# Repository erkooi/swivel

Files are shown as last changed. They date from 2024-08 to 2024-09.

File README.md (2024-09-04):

# Model and animation of an F35B airplane swivel in OpenSCAD

For a video with animations of the swivel and more information please also check my channel "Eric Kooistra - Hobby" on YouTube: https://www.youtube.com/@EricKooistra-Hobby

## 1 3D-printed swivel model
The swivel model consists of four identical tube segments, one as input tube, two for the mid tube, and one as output tube.

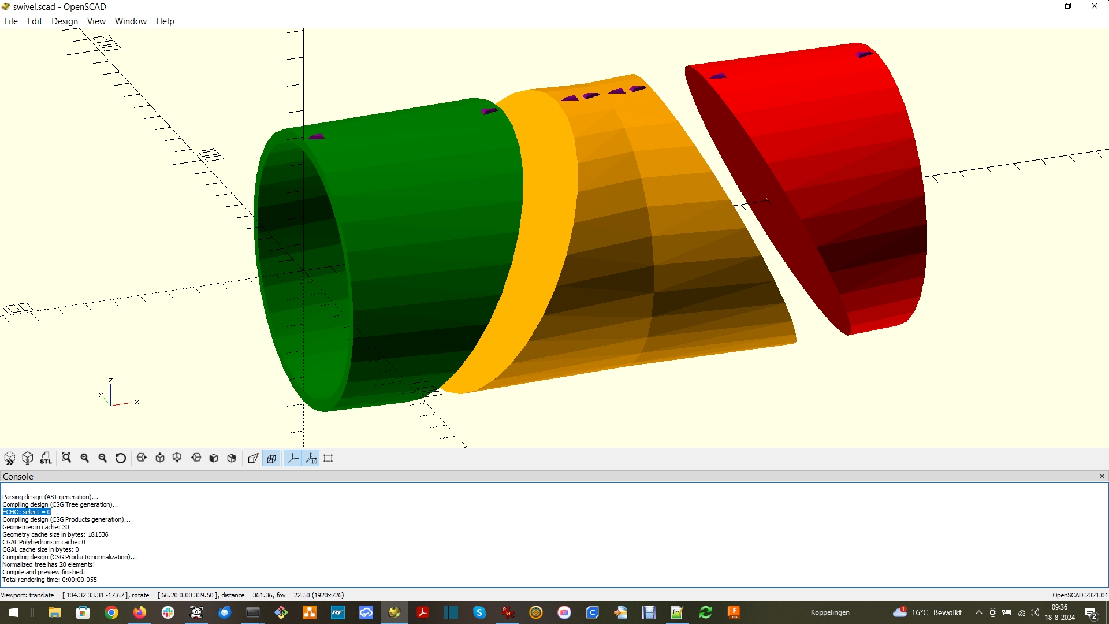
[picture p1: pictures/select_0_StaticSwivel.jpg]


Figure 1.1: Four identical tube segments for swivel model

After 3D printing, the two segments for the mid tube are glued together and then bolted to the input segment and to the output segment. The bolts should be so tight that the tubes maintain their position, but can be rotated manually.

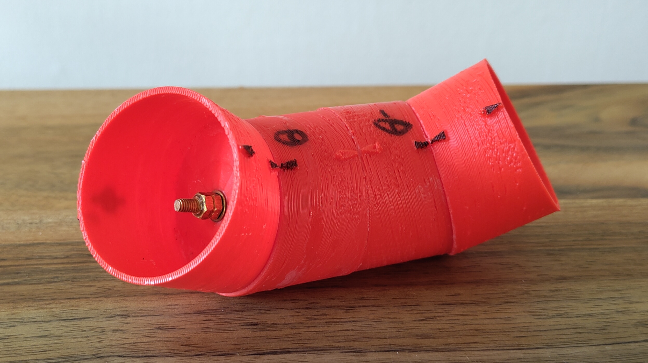
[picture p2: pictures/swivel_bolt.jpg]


Figure 1.2: 3D printed swivel model

In an application of the swivel typically has three slew bearings.
* one slew bearing to connect the input tube to the fixed tube in the airplane, to rotate the swivel in the YZ plane.
* two slew bearings to connect the mid tube to the input tube and to the output tube, to point the swivel between straigt and maximum tilted.

## 2 Swivel model definitions
The swivel is at the tail of an airplane. The airplane is oriented with up in positive Z direction and right in positive Y direction. For forward flight the airplane flies in negative X direction, and the swivel thrust vector points horizontal in positive X direction.

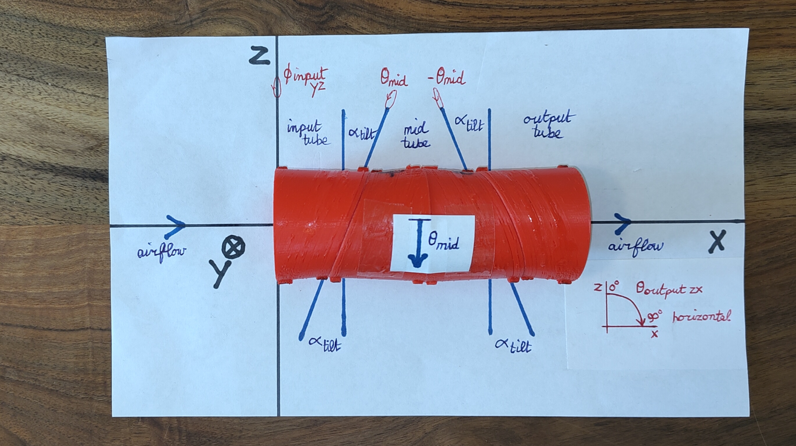
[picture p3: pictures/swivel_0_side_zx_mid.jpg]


Figure 2.1: Straight swivel for forward flight

The alpha_tilt angle beteen the tube segments yields a maximum pointing range of 0 to 4 * alpha_tilt degrees, when the mid tube is rotated by theta_mid = 0 to 180 degrees. For alpha_tilt > 22.5 degrees the swivel output can be pointed slightly forward as well, which makes it possible to use the swivel for pitch control during hovering.

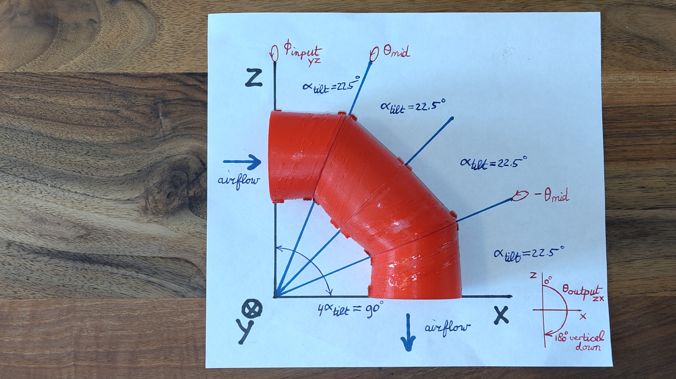
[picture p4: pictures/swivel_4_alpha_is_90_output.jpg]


Figure 2.2: Tilted swivel for hover flight

The swivel is also called 3-bearing swivel nozzle or 3-bearing swivel module (BSM), because it has three bearings: one bearing to rotate the input tube with respect to the fuselage, one bearing to rotate the mid tube with respect to the input tube and one bearing to rotate the output tube with respect to the mid tube.

### 2.1 Coordinates and angles
The XYZ coordinates and corresponding zero angle and positive angle directions are defined as:
```
From https://github.com/erkooi/openscad/libraries/linear_algebra.scad:

* Right-handed coordinates X, Y, Z:
  . right hand fingers point from X to Y points tumb to Z
  . screw from X to Y goes to Z

      z
      |          . angleYZ
      |--- y     . angleZX
     /           . angleXY
    x

* Euler angles
  - https://en.wikipedia.org/wiki/Euler_angles
  - positive rotation about:
    . X-axis from Y to Z = phi, is roll, aileron, banking
    . Y-axis from Z to X = theta, is pitch, elevator, elevation
    . Z-axis from X to Y = psi, is yaw, rudder, heading

* Spherical coordinates P(r, phi, theta)
  - https://en.wikipedia.org/wiki/Spherical_coordinate_system
    . r is radial distance from origin to P
    . phi is angle from X to projection of P in XY plane
    . theta is angle from Z to radial line through P
```

## 3 Swivel control
### 3.1 Input tube rotation (phi_input_yz)
The input tube rotates in the YZ plane. The input tube YZ angle phi_input_yz therefore also directly affects the YZ angle phi_output_yz of the swivel output.

### 3.2 Mid tube rotation (theta_mid)
The mid tube rotates in the tilted plane with the input tube and the output tube rotates in the tilted plane with the mid tube, whereby these rotations are equal but in opposite directions. Thanks to these opposite rotations of the mid tube, all three tubes of the swivel always remain in a common plane, so the swivel output pointing is the same as the pointing of the output tube. The swivel is straight when the angle between the mid tube and the input tube is theta_mid = 0. The swivel is maximum tilted when theta_mid = 180 degrees. Hence the mid tube rotation determines the off center XR angle theta_output_xr between the X-axis and the swivel output pointing.

#### 3.2.1 Counter rotation of input tube
When the mid tube is rotated, then the swivel output also rotates in the YZ plane. To keep the swivel thrust vector pointing of theta_output_xr in a fixed plane, typically the ZX plane, it is therefore necessary to compensate for this side effect by counter rotating the input tube via phi_input_yz. The counter rotation via phi_input_yz then ensures that phi_output_yz remains at 270 degrees when the swivel output is moved between horizontal and maximum tilted down in the ZX plane.

Thanks to the counter input tube rotation by phi_output_yz(theta_mid), the control of the output pointing in the ZX plane via the mid tube rotation, and in the YZ plane via the input tube rotation, become independent.

#### 3.2.2 Positive and negative rotation of mid tube
The mid tube can be rotated in positive theta_mid direction from 0 to +180 or in negative direction from 0 to -180. In both cases the end point positions at theta_mid = 0 and 180 are the same, but the required counter rotation by the input tube is opposite to keep the swivel output in the ZX plane.

### 3.3 Initial swivel orientation
When the swivel is straight (theta_mid = 0), then the YZ angle of the input tube is don't care. However when theta_mid != 0 then phi_input_yz is defined to keep the swivel output in the ZX plane. Therefore for theta_mid = 0 the phi_input_yz angle of the input tube does have to be initalized dependent on the mid tube rotation direction ('positive' or 'negative') and the intended output tube pointing ('down' or 'up') in the ZX plane.

The Figure below shows the swivel model in OpenSCAD. The initial phi_input_yz = 180 for the YZ angle of the long side of the input tube. For positive theta_mid from 0 to +180 the swivel will tilt down and for negative theta_mid from 0 to -180 it will tilt up. Hence for positive theta_mid control the swivel needs to be mounted like shown in the airplane. For negative theta_mid the initial YZ angle of the long side of the input tube would have to be mounted at phi_input_yz = 0, so 180 degrees rotated in the YZ plane compared to the Figure, to have the swivel tilt down.

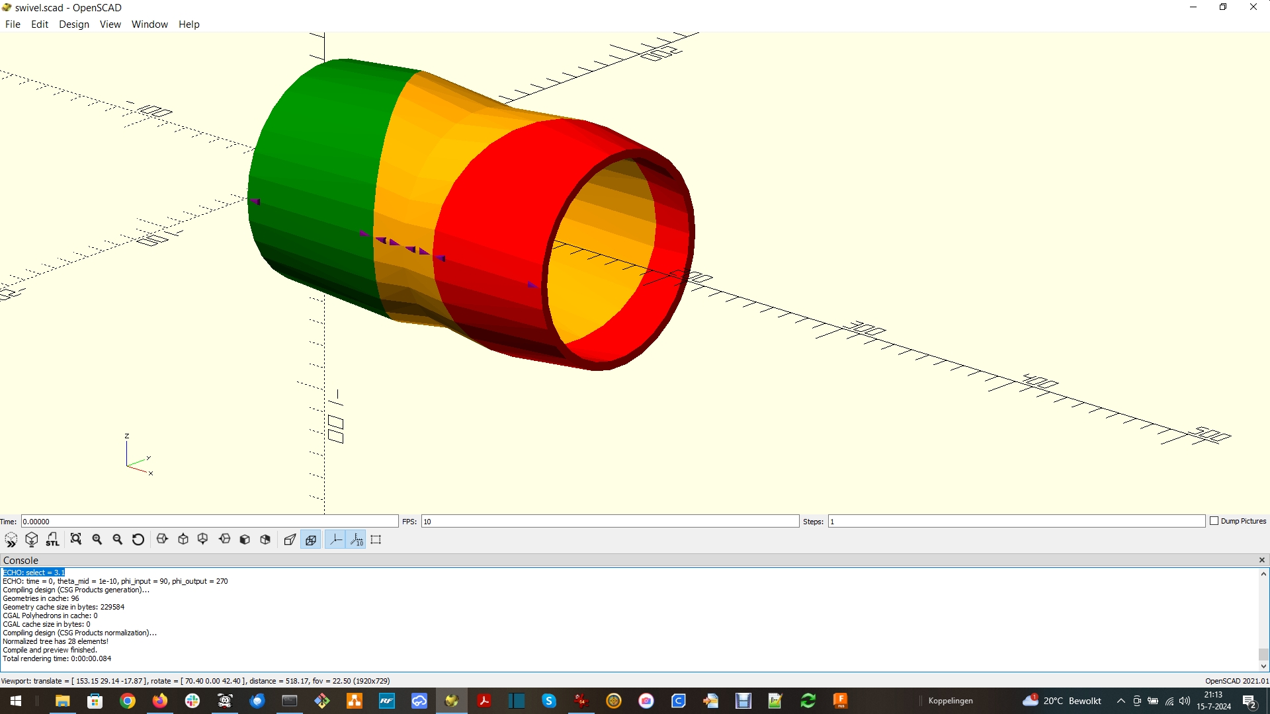
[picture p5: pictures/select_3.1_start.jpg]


Figure 3: Swivel model in OpenSCAD

### 3.4 Swivel output pointing control procedure
1. Choose a swivel output pointing via OutputTube YZ angle and OutputTube XR angle
2. Approximate MidTube angle from requested OutputTube XR angle
3. Approximate InputTube YZ angle from requested OutputTube YZ angle and YZ crosstalk due to MidTube angle

## 4 Operation in an airplane
The swivel is suitable operation in an airplane for:
* forward flight,
* hovering,
* thrust vectoring for yaw and pitch control during hovering,
* transition between forward flight and hovering.

The swivel is not suitable for thrust vectoring for yaw and pitch control during forward flight.

### 4.1 Forward flight
During forward flight the swivel is kept straight. Steering is done by the airplane surfaces (ailerons, elevator and rudder).

### 4.2 Hovering
During hovering the swivel is tilted to vertical down. The airplane can then be kept in balance by controlling the thrust from the swivel output at the back of the plane, another fan at the front of the plane and a fan in each wing.

### 4.3 Thrust vectoring for yaw and pitch control during hovering
The swivel can perform small pointing adjustments around vertical down to have yaw and pitch control during hovering:
* Rotation of the input tube provides steering in the YZ plane for yaw control.
* Rotation of the mid tube provides steering in the ZX plane for pitch control (provided that the swivel has alpha_tilt > 22.5 degrees)

Together the rotation in the YZ plane (so around the X-axis) and the ZX plane (so around the Y-axis) provide smooth control of the swivel output XY angle, similar as with a two-axis gimbal.

### 4.4 Transition between forward flight and hovering
The mid tube rotation provides smooth control between straight swivel and tilted swivel. While rotating the mid tube the input tube can smoothly counter rotate to keep the swivel output in the ZX plane.

### 4.5 Thrust vectoring for yaw and pitch control during forward flight (not suitable)
For smooth thrust vectoring during forward flight it is necessary to be able control the swivel output like a two-axis gimbal. For pitch (= up and down) the swivel output needs to rotate in the ZX plane (so around the Y-axis) and for yaw (= left and right) the swivel output needs to rotate in the XY plane (so around the Z-axis). However this is not possible when the swivel is straight, because:
* Rotation of the input tube occurs in the YZ plane,
* Rotation of the mid tube provides steering in the ZX plane, but only between horizontal and down (not between up, horizontal and down).

The swivel can point to any direction around the X-axis by rotating the mid tube to get the off center XR angle and then abruptly rotating the input tube to get the intended YZ angle. However in a real application the input tube cannot instantaneously reach a new YZ angle. Furthermore rotating the input tube by a full circle to reach all off center pointings would complicate the wiring and construction in a real application. Therefore the swivel is not suitable for thrust vectoring during forward flight.

### 4.6 Control range
* The mid tube needs to be able to rotate over 180 degrees, to transition the swivel between straight and maximum tilt.
* The input tube needs to be able to counter rotate over 90 degrees to compensate for the mid tube rotation, plus some more degrees to facilitate some yaw control.

## 5 Animate swivel movements in OpenSCAD
The swivel model movements are animated in OpenSCAD. The swivel.scad design in OpenSCAD can:

- show the swivel model segments,
- animate transition between horizontal swivel for forward flight, and swivel vertical down for hovering,
- animate small adjustments around swivel vertical down, for pitch (forward - backward) and yaw (left - right) control during hovering.

In addition the swivel model can also animate swivel movements in OpenSCAD that are possible, but that are not suited for use in an airplane:

- animate swivel moving from horizontal to vertical full down to horizontal to vertical full up to horizontal in the ZX plane, to show that this is possible with one rotation of the input tube for every two rotations of the mid tube.
- animate thrust vectoring around swivel horizontal for forward flight, to show that small pointing variations around horizontal require abrupt changes in phi_input_yz.

### 5.1 Files in swivel/openscad
Add library path to OPENSCADPATH environment variable.

* swivel.scad : main program with select options to 3D print, show and animate the swivel
* swivel_functions.scad : functions to calculate the orientation of the swivel
* swivel_functions_unit_test.scad : unit test for swivel_functions.scad
* swivel_assembly.scad : assemble the swivel module from its parts
* swivel_parts.scad : module parts for the swivel, the swivel model consists of four identical segment tubes
* swivel_constants.scad : swivel constants to include

Dependencies:
* openscad/libraries/ from https://github.com/erkooi/openscad

## 6 Analyse swivel movements in Python numpy
The swivel model is formed from four tube segments using **rotate** and **translate** transformations from OpenSCAD or using **multmatrix** for 4D transformation matrices for rotation and translation. The result is identical. These 4D matrix equations from swivel_assembly.scad are then used with Python numpy in swivel_functions.py, for further analysis of the swivel movement and thrust vector pointing in a jupyter notebook at python/swivel.ipynb (also available as python/swivel.html).

### 6.1 Files in swivel/python
Add library path to PYTHONPATH environment variable.

* swivel.ipynb, swivel.html - jupyter notebook to determine harmonic approximation of phi_output_yz(theta_mid) and theta_output_xr(theta_mid)
* swivel_functions.py - functions to calculate the orientation of the swivel, equivalent to swivel_functions.scad
* try_swivel.py - try swivel pointings

## 7. Swivel movement as function of input tube rotation and mid tube rotation
### 7.1 Exact equations for swivel control
The matrix equations that yield the swivel output position, are available as function SwivelOutputPosition() in both swivel_functions.scad and swivel_functions.py. These matrix equations are expanded into gonio formules in SwivelOutputPosition_Gonio(), that is also available in both swivel_functions.scad and swivel_functions.py. This expansion yields a huge formula for the swivel output position as function of swivel dimensions, the rotation of the swivel input tube (phi_input_yz) and the swivel mid tube (theta_mid).

Rotating the mid tube by theta_mid changes the pointing of the output tube. For horizontal pointing theta_mid = 0 and for maximum output tilt theta_mid = 180 degrees. The function phi_output_yz(theta_mid) shows how the phi_input_yz of input tube needs to be counter rotated to keep the swivel output pointing in the ZX plane during transition:

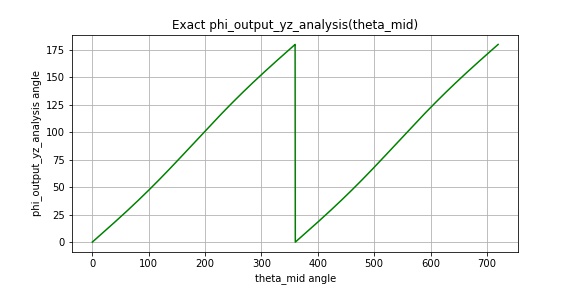
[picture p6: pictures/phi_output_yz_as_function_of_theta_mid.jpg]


Figure 7.1: Exact function phi_output_yz(theta_mid)

The function theta_output_xr(theta_mid) shows how the swivel output pointing depends on the rotation by theta_mid of the mid tube:

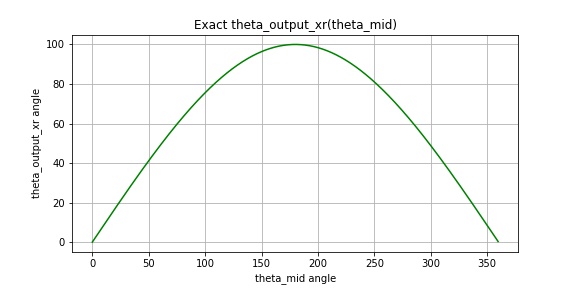
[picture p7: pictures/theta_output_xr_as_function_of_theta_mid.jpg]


Figure 7.2: Excact function theta_output_xr(theta_mid)

### 7.2 Harmonic approximation using the DFT
The exact formula for swivel output control is huge, because it has in the order of hundred terms (see SwivelOutputPosition_Gonio() function in swivel_functions.scad). Therefore it may need to be approximated to be able to implement it in a real time application, using e.g.:

* a precalculated lookup table with values from the exact formula,
* an approximation formula that is close to the exact formula, but much simpler to calculate and that also has an inverse function

The function for phi_output_yz(theta_mid) in Figure 7.1 almost linear, the deviation suggests that adding the first harmonic frequency component deviation yields a good approximation. The function for theta_output_xr(theta_mid) in Figure 7.2 looks like the first halve of a sinus, this suggest that the first harmonic frequency component of concat(theta_output_xr(theta_mid), -theta_output_xr(theta_mid)) yields a good approximation. The harmonic components are obtained using the Discrete Fourier Transform (DFT) for real input signals (rDFT). The f1_ampl of the first harmonic follows from the DFT analysis of the exact formula. With analysis and plots from the swivel.ipynb jupyter notebook this results in:

* Crosstalk between MidTube angle and OutputTube YZ angle:
```
phi_output_yz(theta_mid) ~= theta_mid / 2 - phi_output_yz_f1_ampl * sin(theta_mid)
. for theta_mid in [0:360], to have correct linear term
. phi_output_yz_f1_ampl is a few degrees that approximates the small deviation from linear
```
* OutputTube XR tilt angle due to MidTube angle:
```
theta_output_xr(theta_mid) ~= theta_output_xr_f1_ampl * abs(sin(theta_mid / 2))
. for all theta_mid by using abs(), because XR angle in [0:180]
. theta_output_xr_f1_ampl ~= 4 * alpha_tilt

and inverse:

theta_mid(theta_output_xr) ~=       2 * arcsin(f1_fraction) when MidTube rotation = 'positive'
theta_mid(theta_output_xr) ~= 360 - 2 * arcsin(f1_fraction) when MidTube rotation = 'negative'
. with f1_fraction = theta_output_xr / theta_output_xr_f1_ampl,
. f1_fraction in [0, 1], because theta_output_xr in [0:180] and to fit -1 <= x <= +1 for arcsin(x)
```

### 7.3 Real input DFT support in OpenSCAD
The dft.scad in https://github.com/erkooi/openscad/math implements the real input DFT in OpenSCAD. The implementation uses matrix multiplication and is not optimized like an Fast Fourier Transform (FFT). However with dft.scad it is possible to calculate the harmonic approximation of the swivel control entirely in OpenSCAD.

## 8 Conclusions
- The maximum swivel output angle is four times the tilt angle of the swivel tube segments. Using a tilt angle > 22.5 degrees therefore enables an maximum output angle > 90 degrees, which is necessary for pitch control beyond vertical down during hovering.
- The swivel is suited for forward flight (thrust vector pointing horizontal) and hover flight (thrust vector pointing near vertical down).
- The swivel can transition smoothly between horizontal and vertical down, while keeping the thrust vector pointing in the ZX plane.
- The mid tube needs to rotate between 0 and 180 degrees to transition the swivel pointing between horizontal output and maximum output angle.
- The input tube needs to rotate between 0 and 90 degrees to compensate for rotations of the mid tube and by some more degrees e.g. 10, to provide yaw control.
- The swivel is not suitable for thrust vectoring near horizontal during forward flight, because that would require full circle control and instantaneous control of the input tube rotation.

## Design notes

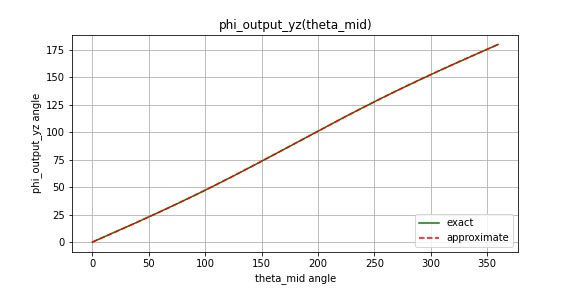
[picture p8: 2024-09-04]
pictures/phi_output_yz_as_function_of_theta_mid2.jpg

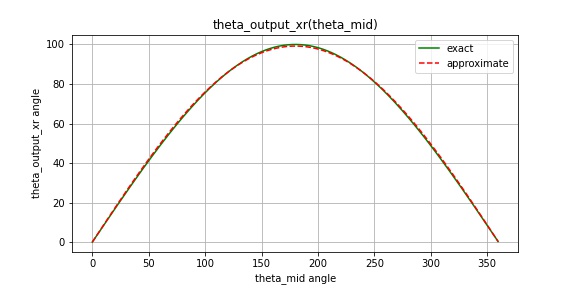
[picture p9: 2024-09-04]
pictures/theta_output_xr_as_function_of_theta_mid2.jpg

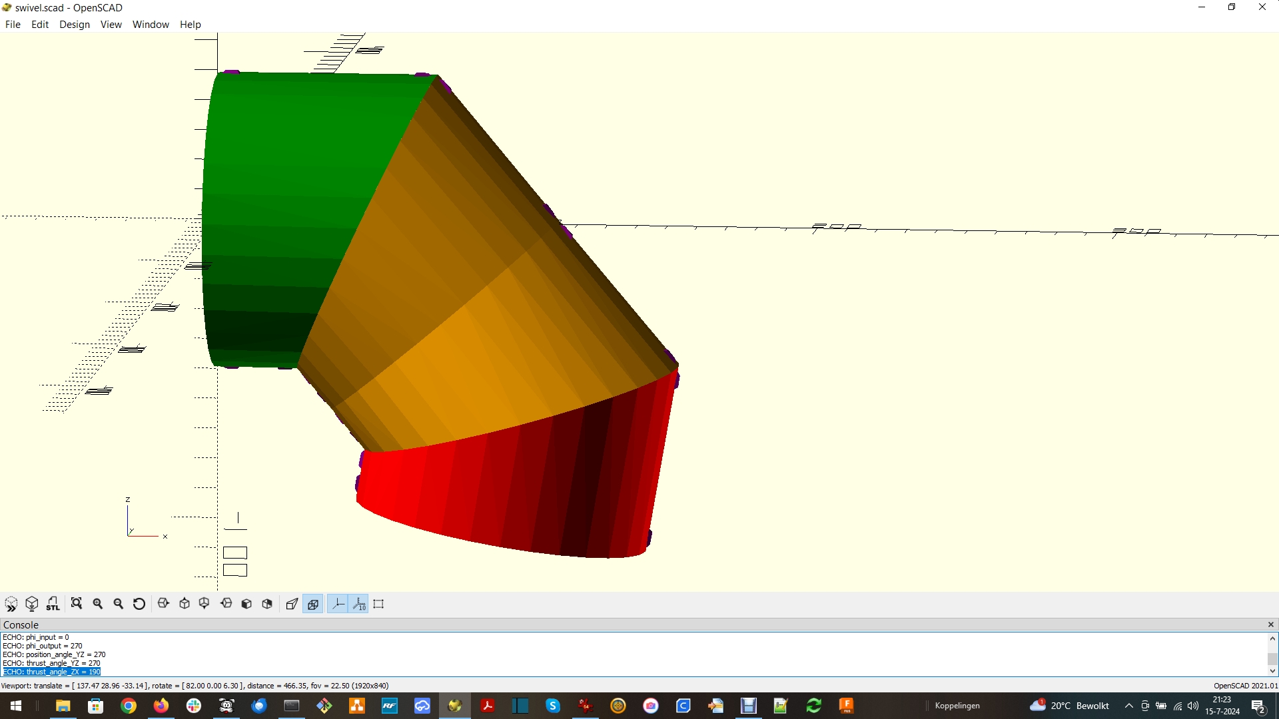
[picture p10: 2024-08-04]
pictures/select_3_full_down_4_alpha_is_100.jpg

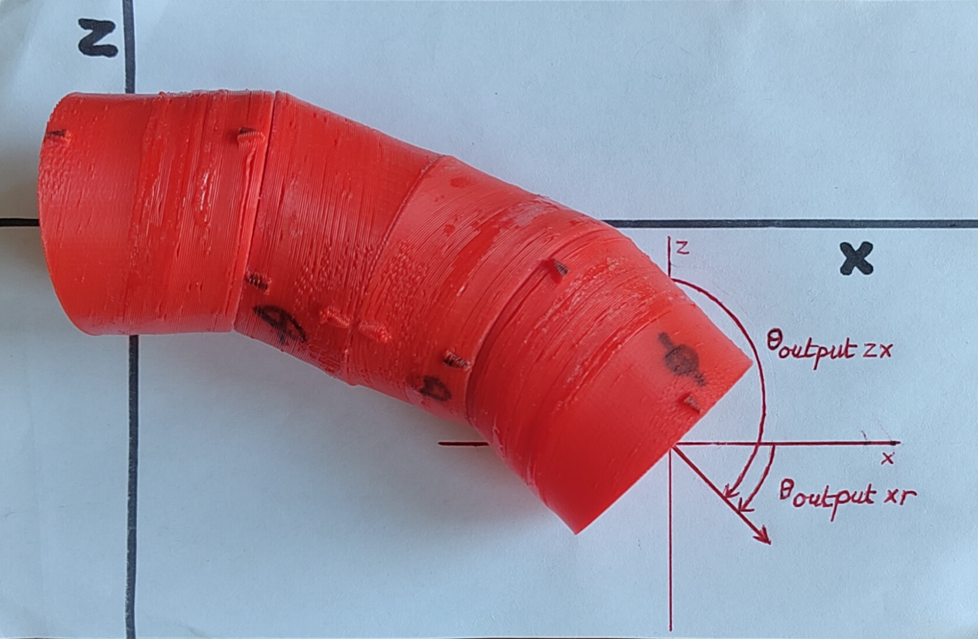
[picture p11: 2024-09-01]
pictures/swivel_45_xr.jpg

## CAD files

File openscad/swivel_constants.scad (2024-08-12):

//------------------------------------------------------------------------------
// Copyright 2024 E. Kooistra
//
// Licensed under the Apache License, Version 2.0 (the "License");
// you may not use this file except in compliance with the License.
// You may obtain a copy of the License at
//
//     http://www.apache.org/licenses/LICENSE-2.0
//
// Unless required by applicable law or agreed to in writing, software
// distributed under the License is distributed on an "AS IS" BASIS,
// WITHOUT WARRANTIES OR CONDITIONS OF ANY KIND, either express or implied.
// See the License for the specific language governing permissions and
// limitations under the License.
//------------------------------------------------------------------------------
//
// Author: E. Kooistra, March 2024
// Purpose: Library of swivel constants to include
// Description:

//------------------------------------------------------------------------------
// General
//------------------------------------------------------------------------------

// Use theta_mid_arr + c_theta_mid_eps to offset theta_mid = 0 for straight
// swivel, which leads to NaN YZ angle. It appears that for SwivelThrustVector()
// c_theta_mid_eps needs to be ~< 1e-7, so la.f_eps = 1e-10 is too small.
c_theta_mid_eps = 1e-7;

// The swivel assembly is constructed with InputTube() long side markers up,
// so with phi_input_yz = 90. However the zero position for the long side 
// markers is better defined at phi_input_yz = 0. Therefore use
// c_phi_input_yz_construction to compensate for this construction offset.
c_phi_input_yz_construction = 90;

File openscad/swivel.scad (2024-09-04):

//------------------------------------------------------------------------------
// Copyright 2022 E. Kooistra
//
// Licensed under the Apache License, Version 2.0 (the "License");
// you may not use this file except in compliance with the License.
// You may obtain a copy of the License at
//
//     http://www.apache.org/licenses/LICENSE-2.0
//
// Unless required by applicable law or agreed to in writing, software
// distributed under the License is distributed on an "AS IS" BASIS,
// WITHOUT WARRANTIES OR CONDITIONS OF ANY KIND, either express or implied.
// See the License for the specific language governing permissions and
// limitations under the License.
//------------------------------------------------------------------------------
//
// Author: E. Kooistra, March 2022
//                      July 2024 updated
// Purpose: Create swivel
// Description:
//   Selections via select_model value to:
//   . Show static model of the swivel parts
//   . Form the swivel with certain orientation
//   . Animate the swivel for range of orientations
//   . 3D print swivel part
//
// Animation:
//   Animation repeatedly loops $t = 0:1/Steps:1, with Steps defined in GUI
//   menu View/Animate.
//   . Use e.g. FPS = 10 frames per second in GUI for movie, or FPS = 1 to see
//     individual frames.
//   . The animation stops when Steps in GUI is set to 0 or left empty.
//   . The animation restarts when Steps in GUI is set to 1 and then set to > 0.
//     E.g. to fill in Steps 80, first fill in the 0 and then the 8 to avoid
//     that the animation first uses Steps 8 and then continues with 80.
//
// Rerun file:
//   . Clear Console using right-mouse Clear
//   . Without animation Openscad reruns after the file is saved, or use
//     Preview F5 icon '>>' to rerun
//
// Coordinates (see openscad/math/linear_algebra.scad)
//
//     z
//     |         . angleYZ
//     |--- y    . angleZX
//    /          . angleXY
//   x

include <math_constants.scad>;
use <linear_algebra.scad>;
use <numscad.scad>;
use <swivel_functions.scad>;
use <swivel_parts.scad>;
use <swivel_assembly.scad>;

//------------------------------------------------------------------------------
// Selections
//------------------------------------------------------------------------------

// select_model:
//   0   StaticSwivel() = 4 times SegmentTube() with x_spacer for exploded view
//   1   SegmentTube() for 3D print
//
//   2   FormSwivel() steer theta_mid with InputTube marker at YZ angle = 0
//   2.1 FormSwivel() animate theta_mid with InputTube marker kept up
//   2.2 FormSwivel() animate phi_output_yz around vertical
//
//   3   FormSwivel() steer theta_mid with OutputTube pointing to phi_output_yz
//   3.1 FormSwivel() animate theta_mid with OutputTube in ZX plane pointing to phi_output_yz_vertical_down
//   3.2 FormSwivel() animate theta_mid with OutputTube in ZX plane pointing to phi_output_yz_vertical_down
//                    and to phi_output_yz_vertical_up
//
//   4   Formswivel() animate OutputTube hovering around phi_output_yz_vertical_down, using rDFT and
//                    harmonics approximation, hover circle as in swivel.ipynb
//   4.1 Formswivel() animate OutputTube hovering around phi_output_yz_vertical_down, using rDFT and
//                    harmonics approximation, hover star pattern (similar as with 8) to show that
//                    thrust vectoring during hover is possible, because the InputTube YZ angle and
//                    MidTube angle control is without jumps.
//   5   Formswivel() animate OutputTube transition between horizontal and phi_output_yz_vertical_down
//                    as 3.1, but using rDFT and harmonics approximation, transition as in swivel.ipynb
//
//   6   FormSwivel() show multiple swivel pointings in one view
//   6.1 DiffSwivel() shows no swivels, verifies DiffSwivel() = FormSwivel - FormSwivel_gonio() == NULL
//
//   7   FormSwivel() animate OutputTube sweep out and back one time, while rotating several times,
//                    to create a spiral pattern
//   8   FormSwivel() animate OutputTube sweep out and back nof_star_points times, while rotating
//                    one time, to create a star pattern, to show that thrust vectoring during
//                    forward flight with near straight swivel is not possible, because it requires
//                    jumps in the control of the InputTube YZ angle.
//   9   Trial
select_model = 3.1;

// select_orientation
//       output_tube_pointing  mid_tube_rotation
//   0     "down"                "positive"
//   1     "down"                "negative"
//   2     "up"                  "positive"
//   3     "up"                  "negative"
select_orientation = 0;

// Segment slope angle
alpha_tilt = 25;

// Number of star points in star form control pattern
nof_star_points = 4;


//------------------------------------------------------------------------------
// Verbosity
//------------------------------------------------------------------------------

// 0   : do only what is needed
// > 0 : do more to e.g. echo status and verify results
verbosity = 1;

if (verbosity > 1) {
    echo("$fa = ", $fa);
    echo("$fs = ", $fs);
    echo("$fn = ", $fn);
}

//------------------------------------------------------------------------------
// Parameters
//------------------------------------------------------------------------------

// Swivel tube segment
R_wall_inner = 45;   // Tube inner radius
d_wall = 4;          // Tube wall thickness
x_input = 50;        // Length of input segment
x_mid = 80;          // Length of middle segment
x_output = 40;       // Length of output segment
x_body = 50;         // Default length of segment for 3D print
x_spacer = 20;       // Segment x_spacer default 0, > 0 to better view them

swivel_tilt_xr_max = SwivelTiltXrMax(alpha_tilt);  // Maximum thrust angle
swivel_tilt_xr_vertical = SwivelTiltXrVertical();

// Optional segment bottom
no_bottom = false;
with_bottom = true;
R_bottom_hole = 1;  // Center drill hole in bottom

// Optional segment rotation markers
L_marker = 8;       // Place markers when > 0
d_marker = 1;       // Depth in the body
h_marker = 1;       // Height outside the body

//------------------------------------------------------------------------------
// Orientation
//------------------------------------------------------------------------------
// Swivel OutputTube() moves from straight to maximum tilted when theta_mid goes
// from 0 to 180 or from 360 to 180 (= 0 to -180). Whether the swivel
// OutputTube() moves down, up, left, right etc., dependents on the InputTube()
// rotation angle phi_input_yz.
output_tube_pointing = select_orientation == 0 || select_orientation == 1
                           ? "down"
                           : "up";

// Positive MidTube rotation angle theta_mid is:
// . from +z to -y, for MidTube with respect to InputTube
// . from +z to +y, for OutputTube with respect to MidTube
// The theta_mid is with respect to InputTube marker up, theta_mid is:
// . 0 for InputTube marker up long side aligned with MidTube short side
// . 0 - 180 OutputTube points to -y, so angle XY < 0
// . 180 for InputTube marker up long side aligned with MidTube long side
// . 180 - 360 OutputTube points to +y, so angle XY > 0
// For theta_mid = 0 or 360 the phi_input_yz angle is don't care and therefore
// undefined. This then causes 180 degrees flip rotation of the MidTube.
// Therefore use theta_mid + f_eps to avoid theta_mid = 0 or 360.
mid_tube_rotation = select_orientation == 0 || select_orientation == 2
                        ? "positive"
                        : "negative";

// InputTube rotation angle phi_input_yz around x-axis in yz plane, phi_input
// is:
// . phi_input_yz = phi_input_yz_for_input_marker_up = 90 for markers on long
//   side of InputTube() on top, so with positive z in the ZX plane (y = 0).
phi_input_yz_for_input_marker_up = PhiInputYzForInputMarkerUp();  // = 90
phi_input_yz_vertical = PhiInputYzVertical(output_tube_pointing);
phi_input_yz_vertical_down = PhiInputYzVertical("down");
phi_input_yz_vertical_up = PhiInputYzVertical("up");

// OutputTube pointing down angle in -z-axis direction in YZ plane
phi_output_yz_vertical = PhiOutputYzVertical(output_tube_pointing);
phi_output_yz_vertical_down = PhiOutputYzVertical("down");
phi_output_yz_vertical_up = PhiOutputYzVertical("up");

theta_output_zx_horizontal = ThetaOutputZxHorizontal();
theta_output_zx_vertical = ThetaOutputZxVertical(output_tube_pointing);
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

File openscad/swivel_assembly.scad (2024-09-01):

//------------------------------------------------------------------------------
// Copyright 2022 E. Kooistra
//
// Licensed under the Apache License, Version 2.0 (the "License");
// you may not use this file except in compliance with the License.
// You may obtain a copy of the License at
//
//     http://www.apache.org/licenses/LICENSE-2.0
//
// Unless required by applicable law or agreed to in writing, software
// distributed under the License is distributed on an "AS IS" BASIS,
// WITHOUT WARRANTIES OR CONDITIONS OF ANY KIND, either express or implied.
// See the License for the specific language governing permissions and
// limitations under the License.
//------------------------------------------------------------------------------
//
// Author: E. Kooistra, March 2022
// Purpose: Library to assemble the swivel module from its parts.
// Description:
//  . Static swivel with spacer between the tube segments
//  . Form swivel from tube segments using rotate and translate from OpenSCAD
//    or using 4D transformation matrices for rotation and translation. The
//    result is identical, so the matrix equations can also be used in Python.

use <linear_algebra.scad>;
use <swivel_parts.scad>;

// The swivel assembly is constructed with InputTube() long side markers up,
// so with phi_input_yz = 90. However the zero position for the long side
// markers is better defined at phi_input_yz = 0. Therefore use
// c_phi_input_yz_construction to compensate for this construction offset, by
// subracting it from the input phi_input_yz in FormSwivel() and
// FormSwivel_Gonio().
include <swivel_constants.scad>;


//------------------------------------------------------------------------------
// Swivel assembly
//------------------------------------------------------------------------------

// Create exploded view of the swivel in horizontal direction, by means of
// x_spacer > 0
module StaticSwivel(x_spacer, x_input, x_mid, x_output, R_wall_inner, d_wall, alpha_tilt,
                    use_bottom, R_bottom_hole, L_marker, d_marker, h_marker) {
    InputTube(x_input, R_wall_inner, d_wall, alpha_tilt, use_bottom, R_bottom_hole, L_marker, d_marker, h_marker);
    translate([x_spacer + x_input, 0, 0])
        MidTube(x_mid, R_wall_inner, d_wall, alpha_tilt, use_bottom, R_bottom_hole, L_marker, d_marker, h_marker);
    translate([x_spacer*2 + x_input + x_mid, 0, 0])
        OutputTube(x_output, R_wall_inner, d_wall, alpha_tilt, use_bottom, R_bottom_hole, L_marker, d_marker, h_marker);
}

// Create the swivel, using translate() and rotate() transformations
module FormSwivel(x_input, x_mid, x_output, R_wall_inner, d_wall, alpha_tilt,
                  use_bottom, R_bottom_hole, L_marker, d_marker, h_marker,
                  phi_input_yz, theta_mid) {
    rotate([phi_input_yz - c_phi_input_yz_construction, 0, 0]) union() {
        InputTube(x_input, R_wall_inner, d_wall, alpha_tilt, use_bottom, R_bottom_hole, L_marker, d_marker, h_marker);
        translate([x_input, 0, 0]) rotate([0, alpha_tilt, 0]) rotate([theta_mid, 0, 0]) rotate([0, -alpha_tilt, 0]) union() {
            MidTube(x_mid, R_wall_inner, d_wall, alpha_tilt, use_bottom, R_bottom_hole, L_marker, d_marker, h_marker);
            translate([x_mid, 0, 0]) rotate([0, -alpha_tilt, 0]) rotate([-theta_mid, 0, 0]) rotate([0, alpha_tilt, 0])
                OutputTube(x_output, R_wall_inner, d_wall, alpha_tilt, use_bottom, R_bottom_hole, L_marker, d_marker, h_marker);
        }
    }
}

// Create the swivel, using 4D matrices
// FormSwivel_Gonio = FormSwivel, but using gonio matrix equations
module FormSwivel_Gonio(x_input, x_mid, x_output, R_wall_inner, d_wall, alpha_tilt,
                        use_bottom, R_bottom_hole, L_marker, d_marker, h_marker,
                        phi_input_yz, theta_mid) {
    mRot_yz(phi_input_yz - c_phi_input_yz_construction) union() {
        InputTube(x_input, R_wall_inner, d_wall, alpha_tilt, use_bottom, R_bottom_hole, L_marker, d_marker, h_marker);
        mTrans(x_input, 0, 0) mRot_zx(alpha_tilt) mRot_yz(theta_mid) mRot_zx(-alpha_tilt) union() {
            MidTube(x_mid, R_wall_inner, d_wall, alpha_tilt, use_bottom, R_bottom_hole, L_marker, d_marker, h_marker);
            mTrans(x_mid, 0, 0) mRot_zx(-alpha_tilt) mRot_yz(-theta_mid) mRot_zx(alpha_tilt)
                OutputTube(x_output, R_wall_inner, d_wall, alpha_tilt, use_bottom, R_bottom_hole, L_marker, d_marker, h_marker);
        }
    }
}


// Create difference of FormSwivel using transfomations and using 4D matrices
// Should result in no object, because FormSwivel() = FormSwivel_Gonio()
module DiffSwivel(x_input, x_mid, x_output, R_wall_inner, d_wall, alpha_tilt,
                  use_bottom, R_bottom_hole, L_marker, d_marker, h_marker,
                  phi_input_yz, theta_mid) {
    difference() {
        FormSwivel(x_input, x_mid, x_output, R_wall_inner, d_wall, alpha_tilt,
                   use_bottom, R_bottom_hole, L_marker, d_marker, h_marker,
                   phi_input_yz, theta_mid);
        FormSwivel_Gonio(x_input, x_mid, x_output, R_wall_inner, d_wall, alpha_tilt,
                         use_bottom, R_bottom_hole, L_marker, d_marker, h_marker,
                         phi_input_yz, theta_mid);
    }
}

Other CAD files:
openscad/swivel_functions.scad
openscad/swivel_functions_unit_test.scad
openscad/swivel_parts.scad

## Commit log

2024-08-04 Add swivel repo for github.
    [swivel.scad, swivel_assembly.scad, swivel_constants.scad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]
2024-08-12 Align scad with py code.
    [swivel.scad, swivel_constants.scad, swivel_functions.scad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]
2024-08-25 Align openscad and python.
    [swivel.scad, swivel_functions.scad, swivel_functions_unit_test.scad]
2024-08-26 Use snr(). Use 1,1,1 in SwivelThrustVector().
    [swivel.scad, swivel_functions.scad, swivel_functions_unit_test.scad]
2024-09-01 Add 6.1 to verify FormSwivel(). Add 4.1 to hover star pattern. Improve SwivelThrustVector().
    [swivel.scad, swivel_assembly.scad, swivel_functions.scad]
2024-09-04 Plot exact and approximate. Add 2.2.
    [swivel.scad, swivel_functions.scad, swivel_functions_unit_test.scad]
